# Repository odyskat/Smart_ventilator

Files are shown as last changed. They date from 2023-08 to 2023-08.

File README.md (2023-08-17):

# Smart_ventilator
## Abstract:
Smart ventilator designed on  window metal bar. Aims to reduce humidity by renewing the air inside a 10 m^3 room  with high humidity at a ~210 m^3/h rate. Needs less than 8 min to renew the air inside the room one time.
Uses a reed switch positioned in the window opening to know when the window is open, then it checks for humidity changes utilizing the shtc3 sensor, and if it reed increased humidity it stars the fans in full power mode until the humidity goes back to normal (previous) levels. When the window is closed, the device goes automatically back to sleep.
The device is powered by a Xiaomi 10000 mAh power bank with two USB A outputs at 5v and 1A, and the fan operates at 12 volts 0.1 A each. For converting the voltage it utilizes a 
variable boost converter set at 12V output. The converter includes a convenient micro USB-in port and connects to the power bank with a standard USB A to micro B cable.

## Device "skeleton":
The device is made from simple PLA or ABS plastic and optionally TPU for the gaskets, everything is 3d printed using simple ender printers. It includes a sensor stand in the back for fastening the sensor, a cable management bay, cable out holes **(which must be filled with standard silicon to achieve water resistance.)**, and screw joints which must be embedded with threaded inserts for plastic. It hangs from a top window metal bar. 
The battery sits outside the casing for easy access and recharging. In the future, a solar panel for battery charging will be added to make the system completely autonomous.

3d printable files included in the folder "for 3d print".

Renders of the device :

Fan_module_with_Bathroom_window_and_fans_v3_2023-Aug-16_12-37-50PM-000_CustomizedView10508488103_jpg

Fan_module_with_Bathroom_window_and_fans_v3_2023-Aug-16_12-38-32PM-000_CustomizedView15031821479_jpg

Fan_module_with_Bathroom_window_and_fans_v3_2023-Aug-16_12-45-48PM-000_CustomizedView307875928_jpg

Fan_module_with_Bathroom_window_and_fans_v3_2023-Aug-16_12-37-13PM-000_CustomizedView29614088936_jpg
## Electronics
### Materials:
1. Arduino nano
2. Adafruit shtc3 sensor
3. DC-DC step up converter
4. Xiaomi redmi power bank 10000 mAh **(instead of Lilypad power supply used only for example purposes in wiring diagrams)**
5. Reed switch
6. 4x Arctic f8 80 mm pst fans

### Wiring:

Smart ventilator arduino nano wiring_bb

Smart ventilator arduino nano wiring_schem

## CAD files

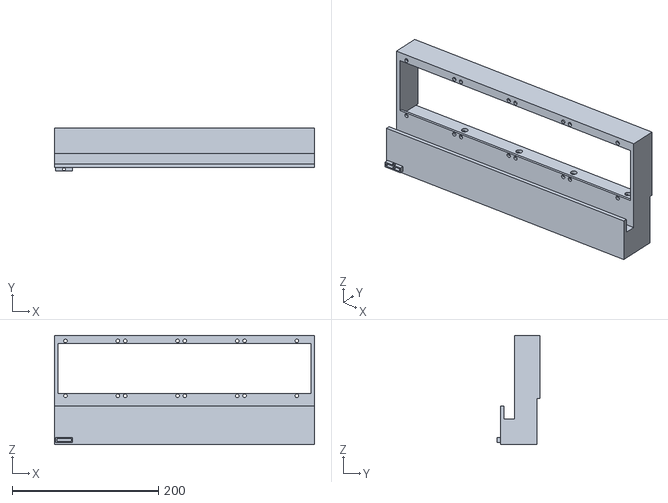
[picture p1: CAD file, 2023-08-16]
for 3d print/Fan skeleton.stl
355.0 x 59.0 x 149.0

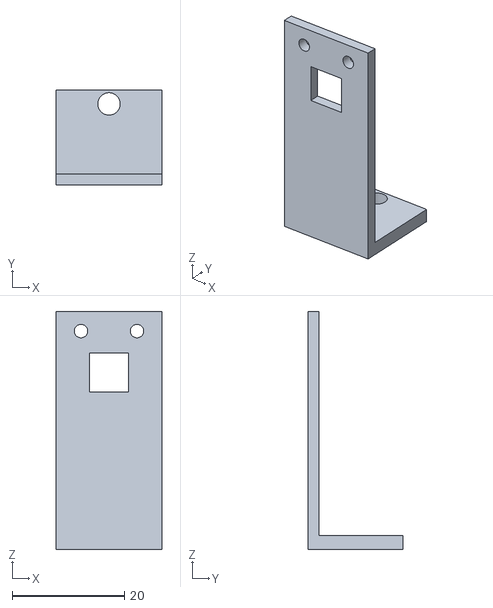
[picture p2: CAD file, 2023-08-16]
for 3d print/Sensor stand.stl
19.0 x 17.0 x 42.5

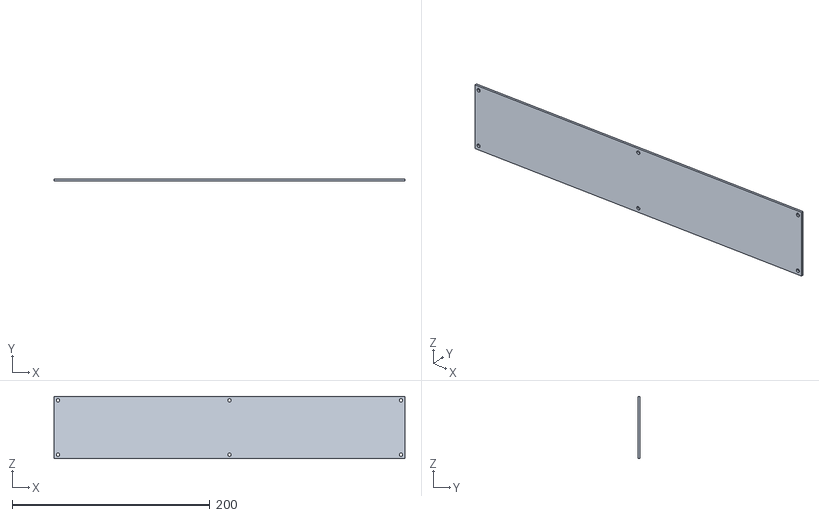
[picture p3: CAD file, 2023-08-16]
for 3d print/Box cap.stl
355.0 x 2.00 x 63.0

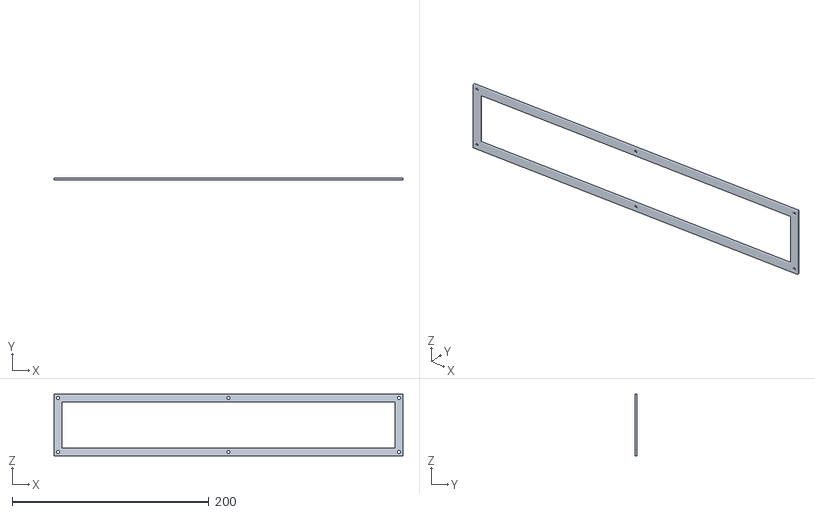
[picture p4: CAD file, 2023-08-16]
for 3d print/Gasket.stl
355.0 x 2.00 x 63.0

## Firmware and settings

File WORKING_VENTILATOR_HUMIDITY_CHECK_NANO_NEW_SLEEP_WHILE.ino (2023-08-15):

// sleep library 
#include "LowPower.h"


// DFRobot SHT - Version: Latest
#include <DFRobot_SHT.h>
#include <DFRobot_SHT40.h>
#include <DFRobot_SHTC3.h>
DFRobot_SHTC3 SHTC3;

//Microcontroller's pwm and timer variables####
int pwmPin = 5;  // the PWM pin the Fan is attached to
int speed = 255;   //starting value, range 0 to 255 becuse of 8bit binary (8digit binary 2^*=256 values)
static unsigned long previousMillis = 0, one_min_Millis=0, ten_min_Millis=0; // Variable to store the previous millis value
unsigned long currentMillis; 
float seconds;
float humold, humold_1_min, humold_10_min; // chose a value over 100 beacause humold 
float dh;
//#####


//SHTC3 sensor variables****
uint32_t id = 0;
float temperature,  humidity;
//****


//reed switch //////////
int DOOR_SENSOR_PIN = 2;  // NANO's d2 pin connected to door sensor's pin and interrupt capable
int doorState;
///////////////////////

//Sleep related variables---------------------------

// Use pin 2 as wake up pin
const int wakeUpPin = DOOR_SENSOR_PIN;
int num=0;
int numloop=0;
//doorstate variable used by sleep function already declared in reed switch related variables
volatile bool entered_sleep;
//-----------------------------------------------------------

//extra variables that are integrated in the cloud version of the IDE!!!!!

float hum;
float temp;

//!!!!!!!!!!!!

// Fan operating-humidity checking variables^^^^^^^^^^^^^^^^^^^^^^^^^
unsigned long time_in_while, time_started;
float hum_start;
bool closed_door_in_while=false;


//^^^^^^^^^^^^^^^^^^^^^^^^^^^^^^^^^^^^^^^^^^^^^^^^^^^^^^^^^^^^^^^^^^^



//Sleep related function--------------------- needs to be before void loop

void wakeUp()
{
  Serial.println("***************************");
  Serial.print("eisodos sthn wake up noymero = ");
  Serial.println(num);
  Serial.println("***************************");
  num=num+1;

}

//-------------------------------------------


void setup() {
  // put your setup code here, to run once:

 // Initialize serial and wait for port to open:
  Serial.begin(9600);
  // This delay gives the chance to wait for a Serial Monitor without blocking if none is found
  //delay(3000)

/*START DFROBOT SHTC3 SENSOR CODE ON VOID SETUP!!! */

  SHTC3.begin();
  SHTC3.wakeup();/*SHTC3 is set to sleep mode by default. Please wake it up before use. Use SHTC3.sleep() to let SHTC3 enter sleep mode; SHTC3 stops working in sleep mode*/

  while ((id = SHTC3.getDeviceID()) == 0) {
    Serial.println("ID retrieval error, please check whether the device is connected correctly!!!");
    delay(1000);
  }

  delay(1000);
  Serial.print("id :0x"); Serial.println(id, HEX);
  Serial.println("************************************************ start ***********");

  /*END DFROBOT SHTC3 SENSOR CODE ON VOID SETUP!!! */

//#########
pinMode(pwmPin, OUTPUT);  // declare pin 23 to be an output:
//#########

/////////////reed switch
 pinMode(DOOR_SENSOR_PIN, INPUT_PULLUP); // set ESP32 pin to input pull-up mode
/////////////

// //sleep relateed------------------- not needed pin d2 is already in input pullup mode from reed switch 

// pinMode(wakeUpPin, INPUT_PULLUP);   given for explanatory purposes

// //---------------------

}

void loop() {
  // put your main code here, to run repeatedly:

doorState = digitalRead(DOOR_SENSOR_PIN); // read state if HIGH (equals 1) door is open if LOW (=0) closed

// Sleep related --------------------------

  // Allow wake up pin to trigger interrupt on high.
    attachInterrupt(digitalPinToInterrupt(2), wakeUp, HIGH);
    
  Serial.println("----------------------------------");
  Serial.print("nuber of iserts to loop function = ");
  Serial.println(numloop);
  Serial.println("----------------------------------");
    
    numloop=numloop+1;

              // doorState = digitalRead(wakeUpPin); not needed given for clarification purposes

    if (doorState==LOW) { //  Almost reduntant with 3rd else if statement in humidity check if loop, could ommit that else if paragraph

    entered_sleep= true;

      analogWrite(pwmPin, 0); // set the speed (duty cycel from 0 to 255 see aboveve comments) of pwm now is maxxed out
      humold=0; // if window is closed opened fast and humold has reached hum value the difference hum-humold won't be great enough to enter the if loop
      Serial.println("Going to sleep");

    LowPower.powerDown(SLEEP_FOREVER, ADC_OFF, BOD_OFF);

    }

    else {
    entered_sleep= false;
    }
    // Disable external pin interrupt on wake up pin. not needed given for clarification purposes
    //detachInterrupt(0); 

 Serial.println("%%%%%%%%%%%%%%%%%%%%%%%%%%%%%%%%%%%%%%%%%%%%%%%%%%%%%%%%%%%%%%%%%");

 Serial.print("entered sleep =  ");
  Serial.println(entered_sleep);

 Serial.println("%%%%%%%%%%%%%%%%%%%%%%%%%%%%%%%%%%%%%%%%%%%%%%%%%%%%%%%%%%%%%%%%%");
//-------------------------------



/////////////reed switch reading doorstate above the sleep section!/////////////////////////////////

        // doorState = digitalRead(DOOR_SENSOR_PIN); // read state if HIGH (equals 1) door is open if LOW (=0) closed

 if (doorState == HIGH) {
    Serial.println("The door is open");
    Serial.print("high value=");
    Serial.println(doorState);
  } else {
    Serial.println("The door is closed");
    Serial.print("low value=");
    Serial.println(doorState);
  }
///////////////////////////////////////////////////////////////////////////////////////////


 /**

         mode  Configure sensor working mode, vary among different sensors
               SHTC3：
                       PRECISION_HIGH_CLKSTRETCH_ON                              Clock Stretching Enabled
                       PRECISION_HIGH_CLKSTRETCH_OFF                             Clock Stretching Disabled
                       PRECISION_LOW_CLKSTRETCH_ON                               Clock Stretching Enabled & Low Power
                       PRECISION_LOW_CLKSTRETCH_OFF                              Clock Stretching Disabled & Low Power
  */
  temperature = SHTC3.getTemperature(/*mode = */PRECISION_LOW_CLKSTRETCH_OFF);
  /**

        mode  Configure sensor working mode, vary among different sensors
              SHTC3：
                      PRECISION_HIGH_CLKSTRETCH_ON                              Clock Stretching Enabled
                      PRECISION_HIGH_CLKSTRETCH_OFF                             Clock Stretching Disabled
                      PRECISION_LOW_CLKSTRETCH_ON                               Clock Stretching Enabled & Low Power
                      PRECISION_LOW_CLKSTRETCH_OFF                              Clock Stretching Disabled & Low Power
  */
  humidity = SHTC3.getHumidity(/*mode = */PRECISION_LOW_CLKSTRETCH_OFF);

  if (temperature == MODE_ERR) {
    Serial.println("Incorrect mode configuration to get temperature");
  } else {
    Serial.print("Temperature :"); Serial.print(temperature); Serial.println(" C");
  }
  if (humidity == MODE_ERR) {
    Serial.println("The mode for getting humidity was misconfigured");
  } else {
    Serial.print("Humidity :"); Serial.print(humidity); Serial.println(" %RH");
  }
  /**
        mode  Configure sensor working mode
                      PRECISION_HIGH_CLKSTRETCH_ON                              Clock Stretching Enabled
                      PRECISION_HIGH_CLKSTRETCH_OFF                             Clock Stretching Disabled
                      PRECISION_LOW_CLKSTRETCH_ON                               Clock Stretching Enabled & Low Power
                      PRECISION_LOW_CLKSTRETCH_OFF                              Clock Stretching Disabled & Low Power
  */
  //if(SHTC3.getTemHum(temperature,humidity,PRECISION_HIGH_CLKSTRETCH_ON)){
  //  Serial.print("Temperature :"); Serial.print(temperature); Serial.println(" C");
  //  Serial.print("Humidity :"); Serial.print(humidity); Serial.println(" %RH");
  //} else{
  //  Serial.println("Pattern configuration error");
  //}
  // delay(10000);  // ##########################changed delay to 10 sec

  Serial.println("----------------------------------------");
  
  temp = temperature;
  hum = humidity;

  
  //########
  currentMillis = millis(); // Get the current value of millis()
  seconds = currentMillis / 1000.0; // Convert millis to seconds as a floating-point number
  
  Serial.print("Milliseconds: ");
  Serial.print(currentMillis);
  Serial.print(" | Seconds: ");
  Serial.println(seconds);
  
  // chech for milli() reset that occurs 49 days and 17 hours after remaining consdtantly on max millis number in mllisecods 4.294.967.295 ///////////////////////////////////
  // if millis is reset revert all time related variables to 0

  if (previousMillis > currentMillis) {
    previousMillis=0;
    one_min_Millis=0;
  }
////////////////////////////////////////////




  // Check if 60 seconds have passed
  if (currentMillis - previousMillis >= 10000) {
    previousMillis = currentMillis; // Update the previousMillis value
    Serial.println("10 seconds have passed!");
    // Add your code here to execute every 60 seconds
    humold=hum;
    Serial.print("humold: ");
    Serial.println(humold);
  }
  // else if (currentMillis - one_min_Millis >= 60000) {
  // one_min_Millis = currentMillis; // Update the previousMillis value
  // humold_1_min=hum;
  // Serial.println("1 min have past");
  // }
  // else if (currentMillis - ten_min_Millis >= 600000) {
  // ten_min_Millis=currentMillis;
  // humold_10_min=hum;
  // Serial.println("10 min have past");
  // }

  dh=hum-humold;
    
    Serial.print("dh=hum-humold= ");
    Serial.println(dh);
  

// IF HUMIDITY RISES dh>5 , NOT THE FIRST ENTERING HUMOLD!=0, AND WINDOW OPEN doorstate=1

  if (abs(dh)> 5 && humold!=0 && doorState==HIGH) {
    
   Serial.println("ikanapoieitai h synuhkh 1: ");
    Serial.println("*******************");

    hum_start=humold;   // requires humold to be measured relatively fast <=30 sec to make sense
    
  
      //I keep the starting value of humidity when the increase was detected and run the fan until the humidity returns to it, or 2 hours have passed. if millis() returns to zero time in  while <0 exit while.
      open_close_door_fast:
      time_started=millis()-1000;
      do {
       hum = SHTC3.getHumidity(/*mode = */PRECISION_LOW_CLKSTRETCH_OFF);   //re-neasuring humidity inside the while loop
       time_in_while=millis()-time_started;

       Serial.println("ikanapoieitai h sunthiki 1 kai to whlile tis: ");
       Serial.println("$$$$$$$$$$$$$$$$$$$$$$$$$$$$$$$$$$$$$$$$");
       analogWrite(pwmPin, speed); // set the speed (duty cycel from 0 to 255 see aboveve comments) of pwm now is maxxed out

       doorState = digitalRead(DOOR_SENSOR_PIN);
              if (doorState==LOW) {
                closed_door_in_while=true;
                break;
              }
              else {
                closed_door_in_while=false;
              }
      } while (hum-hum_start>5 && time_in_while<7200000 && time_in_while>0);

  analogWrite(pwmPin, 0);
  doorState = digitalRead(DOOR_SENSOR_PIN);
  }

    /////// if  windwow closed fast humold gone 0, then opened fast dh~0 ///////
  
    else if (doorState==HIGH  && closed_door_in_while==true && hum-hum_start>5) {
        //return closed_door to false 
        closed_door_in_while=false;
         Serial.println("sunthiki 2");
          Serial.println("+++++++++++++++++++++++++++++++++++++++++++++++++++");
        goto open_close_door_fast;

    }  

        ////////// if windwow closes/////////
    else if (doorState==LOW) {
      analogWrite(pwmPin, 0); // set the speed (duty cycel from 0 to 255 see aboveve comments) of pwm now is maxxed out
      humold=0; // if window is closed opened fast and humold has reached hum value the difference hum-humold won't be great enough to enter the if loop
      Serial.println("sunthiki 3");
      Serial.println("_________________--------____________________________--------___________________");

    }


}
